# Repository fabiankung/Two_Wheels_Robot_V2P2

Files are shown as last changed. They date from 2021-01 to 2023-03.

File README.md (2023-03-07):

# Two-Wheels_Robot_V2P2 
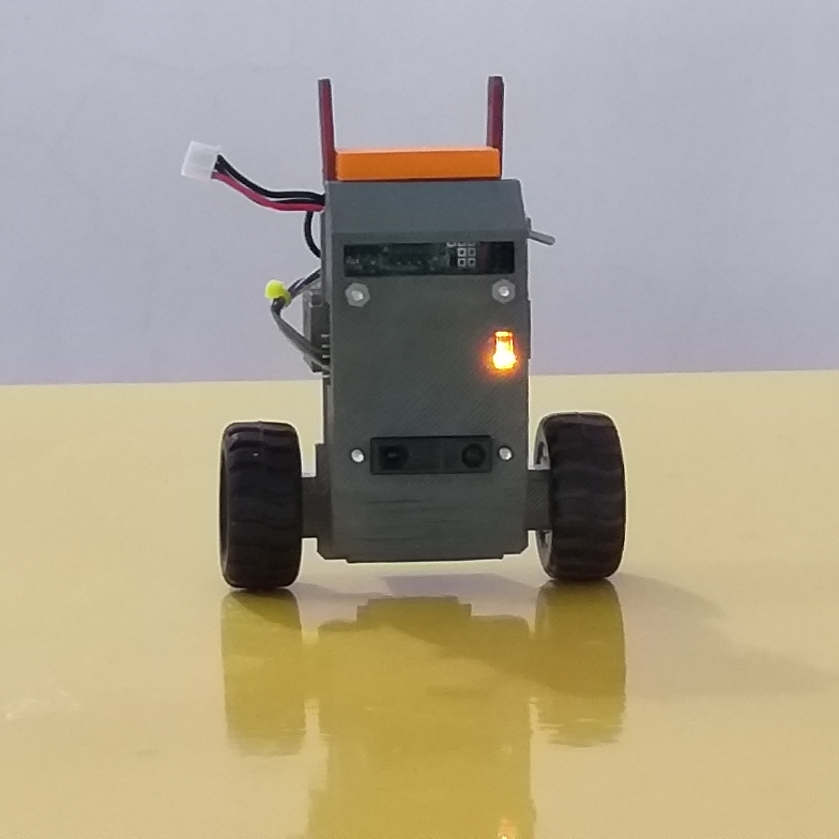
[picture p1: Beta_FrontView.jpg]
Robot Beta Version

V2P2 is a small two-wheels self-balancing mobile robot platform. It contains a single-core on-board computer as the robot controller. The robot controller handles low-level process such as sampling and processing of sensors output, implementing discrete state feedback control to balance the robot body upright and perform secondary tasks such as moving forward, turning etc. User can communicate with the robot controller through a UART port, at 3.3V CMOS logic, baud rate at 57600 bps. A simple two-way protocols allow the user controller to send instructions to the robot controller to perform simple tasks, for instance asking the robot to move at constant linear speed, turn, drive RC servo motors (the system can support up to 4 RC servos), beep a sound and many more. Thus using this robot platform, in combination with an external controller of the user, an intelligent robot system can be constructed. The external controller can be any micro-controller board capable of working with 5V supply and consuming not more than 100 mA current. Examples are Arduino Nano, Micro, Mini-Pro and Arduino Pro-micro.

In this repository, the following files are provided:
1. Getting started guide.
2. Serial communication protocol between the Robot Controller and User Controller.
3. Using Arduino Nano or Micro as the user controller, examples to communicate with the Robot Controller.
4. Andriod APK file for apps to control the V2P2 robot platform directly via Bluetooth.
5. 3D STL files of the mechanical design.
6. The schematic and PCB layout of the main circuit board. The PCB is a 4-layers board.
7. The firmware for the micro-controller.

More details will be provided in future [To do: wiring diagram].
For more robot videos please see: https://www.youtube.com/@fkungms/videos

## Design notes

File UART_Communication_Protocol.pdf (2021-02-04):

Version: 0.991
Last Update: 4 Feb 2021

/// Baud Rate: 57600 (default) or 115200.
/// Data packet: 8-bits, 1 stop bit and no parity bit.
/// --- Command packet from External Controller (EC) ---
/// [Command] + [Argument1] + [Argument2] + [Argument3] + [Argument4] + [Newline Character] /// The Newline character corresponds to 0x0A.
///
/// --- Reply to EC ---
/// If [Command] is G:
/// [Descripon] + [Hundredth] + [Tenth] + [Digit] + [Newline Character]
/// Where [Descripon] indicates the type of parameters being reported back. ///
/// Else:
/// "OK" or "NO", each string ends with [Newline Character]

Notes:
[ ] – Denotes a byte (8-bits unsigned).
[‘a’] – Denotes sending one byte, with the ASCII value of character a.
[3] + [5] – Denotes sending two bytes, first byte has a value of 3, and second byte a value of 5.
[*] – Don’t care, the value in this byte is not used, can just set it to 0.
Master | Slave | Remarks
[‘S’]+[t1]+[t2]+[t3]+[Vol]+[‘\ n’] Example: Beep tones 1, followed by 6, and 2, at volume seng 5. "S1625" | OK NO | Beep a series of 3 tones. t1, t2, t3 = ‘1’ to ‘9’, ‘1’ corresponds to lowest pitch, and ‘9’ to the highest pitch. Vol = Volume, ‘0’ to ‘5’, ‘0’ turns off the buzzer, ‘5’ is the highest volume.
[‘X’]+[*]+[*]+[*]+[*]+[‘\n’] Example: "X0000" | OK NO | Cancel all movments, stop the robot if it is moving or turning.
[‘F’]+[D]+[S0]+[*]+[*]+[‘\n’] Example: Move forward at slow speed. "F+100" | OK NO | Move at fix velocity. D = Direcon, ‘-’ for backward, any other value for forward. S0 = Speed seng, from ‘1’ (slow) to ‘4’ (very fast).
[‘M’]+[ID]+[D]+[A1]+[A0]+[‘\ n’] Example: Turn motor 0 sha to +10 degrees. "M0+10" | OK NO | Set servo motor to a specific absolute angle given by A1, A0. ID = Motor ID, currently support 0 to 2 (3 motors) D = Direcon, ‘-’ or any other values for ‘+’, with respect to center posion of motor sha. A1 = turn degree, tenth, ‘0’ to ‘9’. A0 = turn degree, unit, ‘0’ to ‘9’.
[‘D’]+[ID]+[D]+[A0]+[*]+[‘\n’] Example: Turn motor 0 sha | OK NO | Set servo motor to A1 degree relave to current sha posion. ID = Motor ID, current support 0 to 2.

1

to +8 degrees from current posion. "D0+80" | | D = Direcon, ‘-’ or any other values for ‘+’, with respect to current posion of motor sha. A0 = relave turn degree, unit, ‘0’ to ‘9’.
[‘T’]+[D]+[A2]+[A1]+[A0]+[‘\ n’] Example: Turn le 5 degrees. "T+005" | OK NO | Turn by a fix degree. D = Turn direcon, ‘-’ right, any other value le. A2 = turn degree, hundreth, ‘0’ to ‘9’. A1 = turn degree, tenth, ‘0’ to ‘9’. A0 = turn degree, unit, ‘0’ to ‘9’.

[‘G’]+[P]+[*]+[*]+[*]+[‘\n’]

Example: Request robot
plaorm to send back binary packet containing robot vital parameters.
"Gb000"

For P = ‘D’, ‘B’, ‘F’,
‘V’, ‘A’:
[P]+[V2]+[V1]+[V0]+
[‘\n’]

Where
V2 = Hundredth, ‘0’
to ‘9’.
V1 = Tenth, ‘0’ to ‘9’.
V0 = Unit, ‘0’ to ‘9’.

For P = ‘R’:
“OK” or “NO”

For P = ‘b’:
‘b’ (byte0) +
[Robot_Mode*]
(byte1) +
[Tit angle -127 to +
127] (byte2) +
[Heading upper 8
bits](byte3) +
[Heading lower 8
bits](byte4) +
[Front distance
sensor output, 0-
255mm](byte5) +
[Distance move
upper 8 bits](byte6)
+
[Distance move
lower 8 bits](byte7)

Get robot plaorm parameters. The values return depends on the nature of hardware on the robot.
P = Type of parameter:
‘D’ – Front distance sensor output, 0 to 255. ‘B’ – Baery level, 0 to 255.
‘F’ – Firmware version. Three characters.
‘R’ – Robot plaorm status, “OK” or “NO”. ‘A’ – Tilt angle, “-99” to “+99” in degree.
‘V’ – Wheels average velocity, “-99” to “+99”. 20 units = 1.0 revoluon per second.
‘b’ – Send robot plaorm parameters in binary packet instead of ASCII characters.

*bit3-0 represents the Robot Mode. Bit4 indicates whether Robot Controller is in manual (0) or auto mode (1). Bit 5 indicates whether the Robot plaorm collides
with object or not (based on stability indices signature).
Bit 6 indicates whether the Robot plaorm move or not, either voluntarily or involuntarily.

2

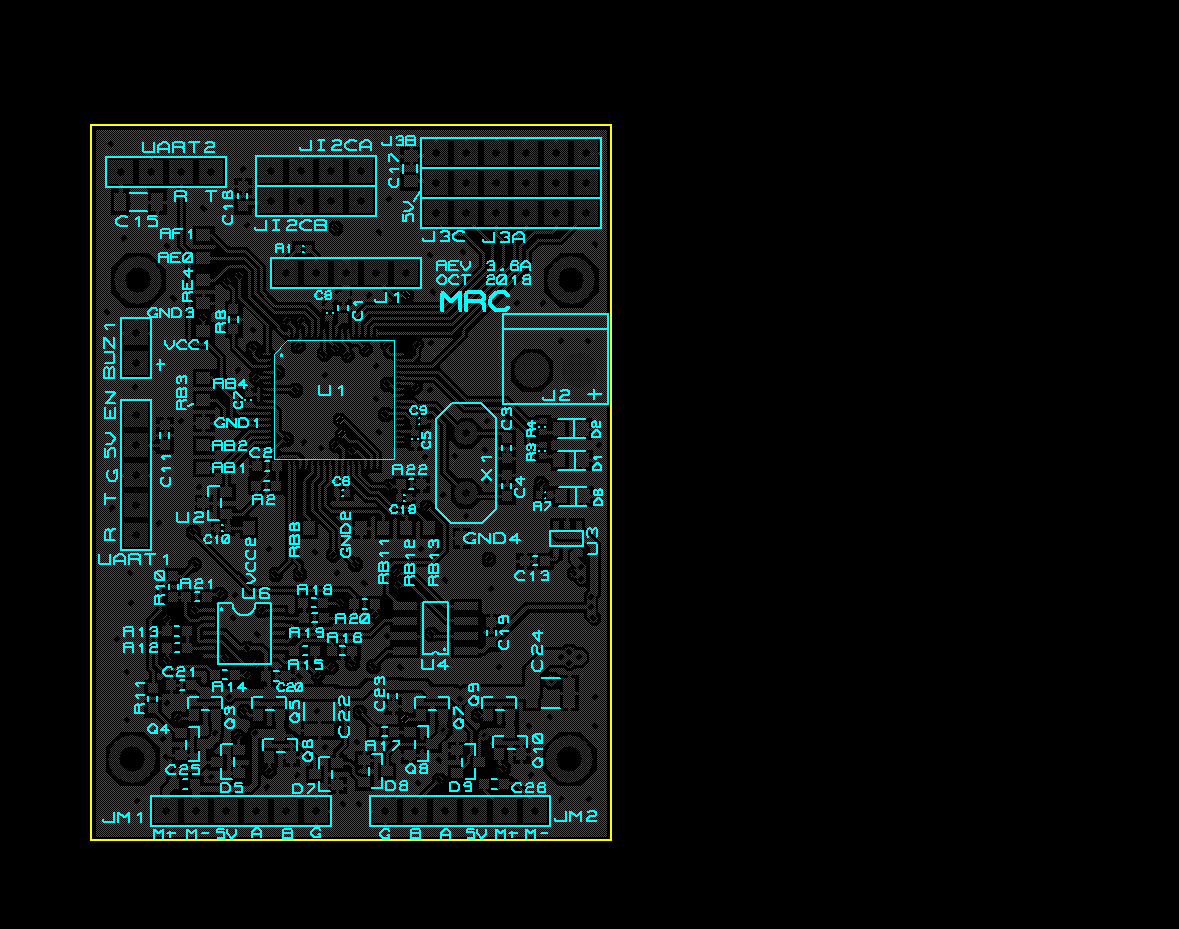
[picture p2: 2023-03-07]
Schematic_PCB/PCB_Top.bmp

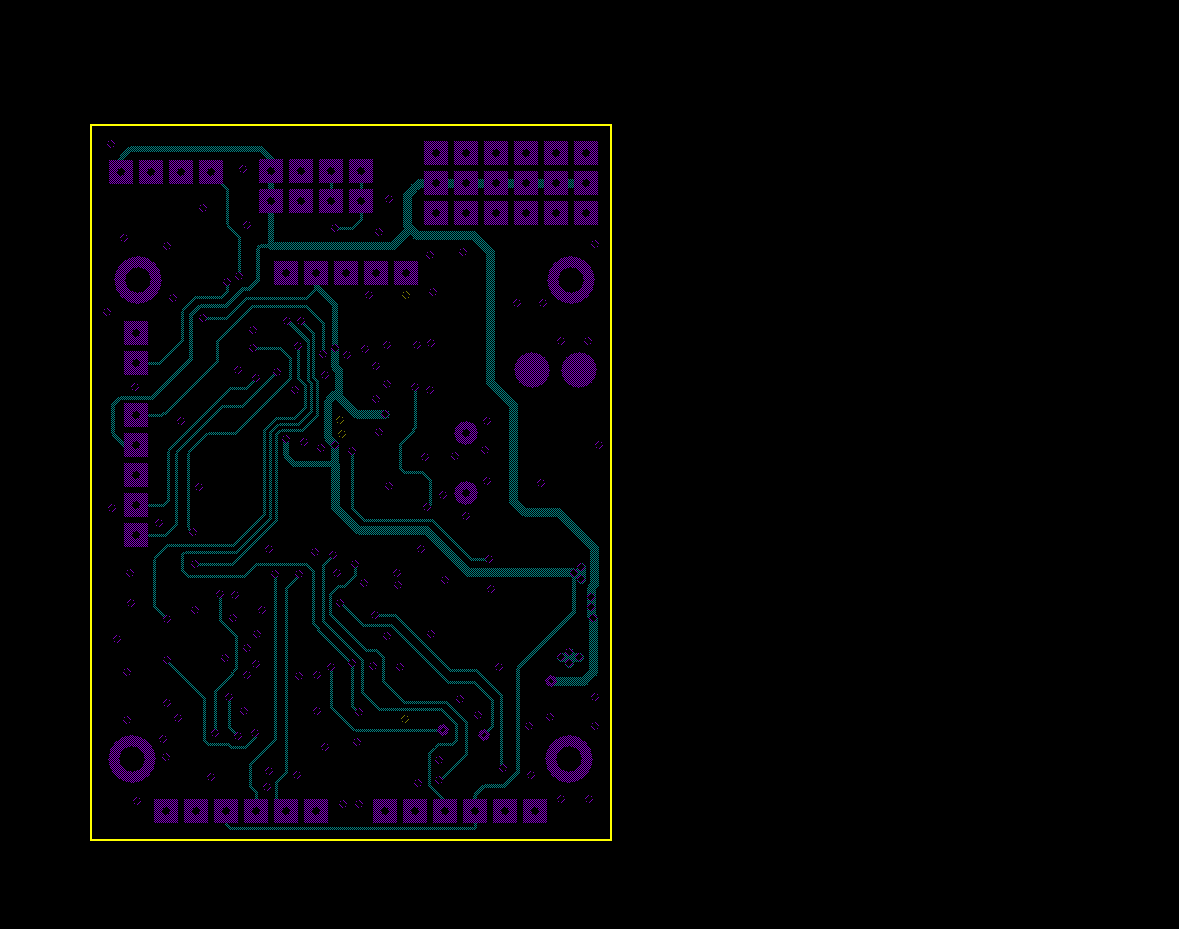
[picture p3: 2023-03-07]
Schematic_PCB/PCB_Inner2.bmp

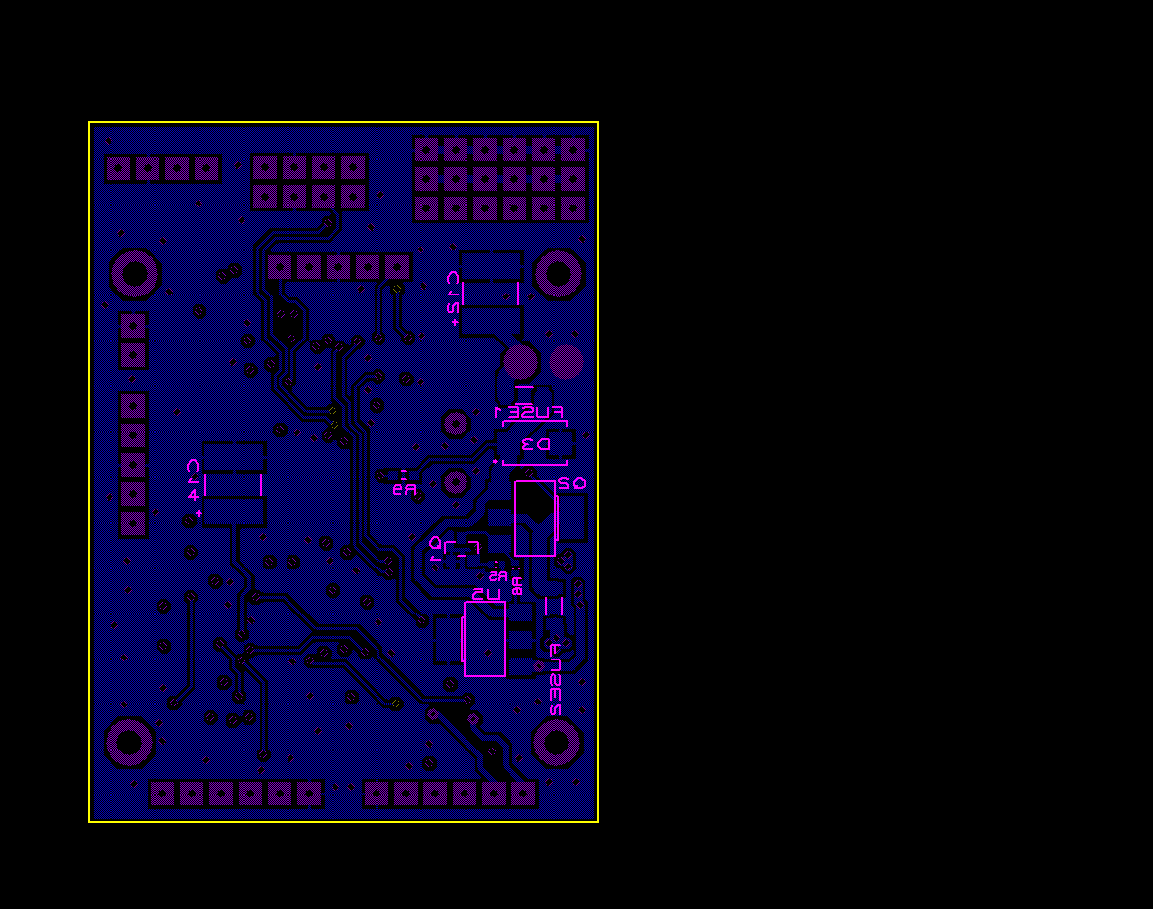
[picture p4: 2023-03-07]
Schematic_PCB/PCB_Bottom.bmp

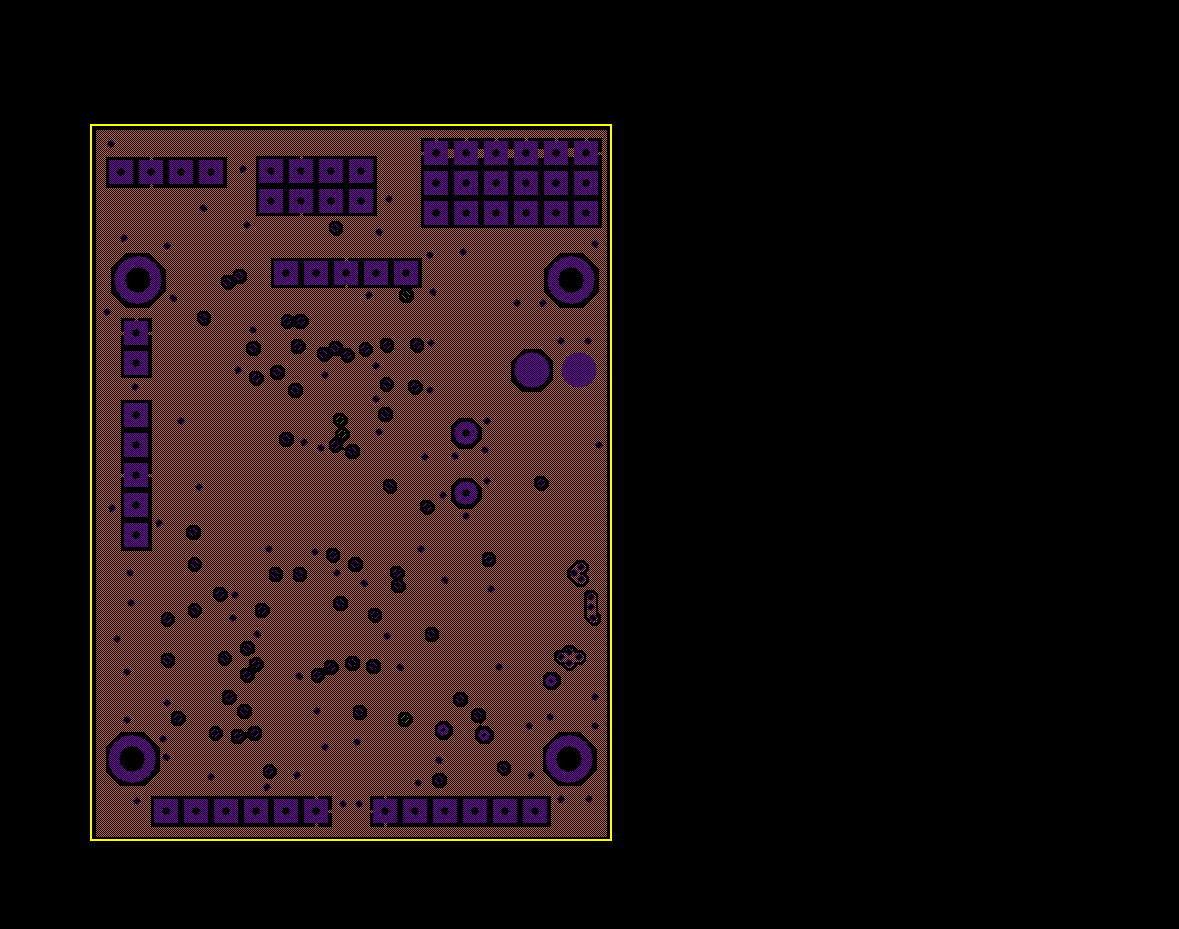
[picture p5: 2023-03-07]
Schematic_PCB/PCB_Inner1.bmp

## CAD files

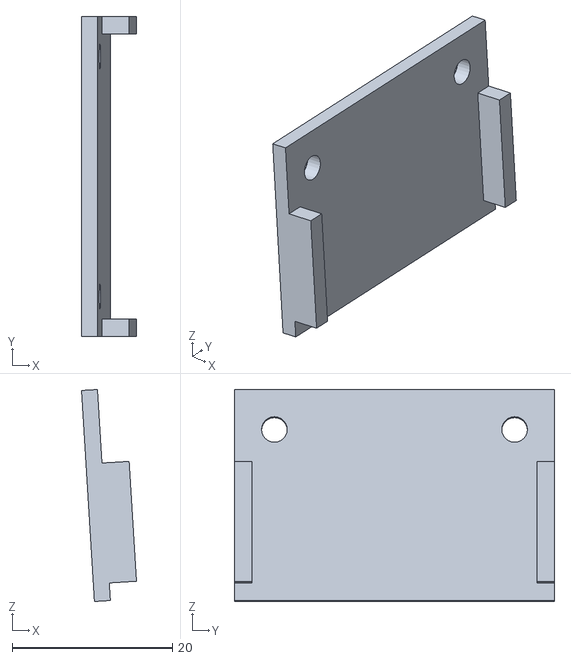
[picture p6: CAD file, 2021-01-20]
3D_Printer_Designs/Main_Body_RevB1_Top.stl
6.87 x 40.0 x 26.5

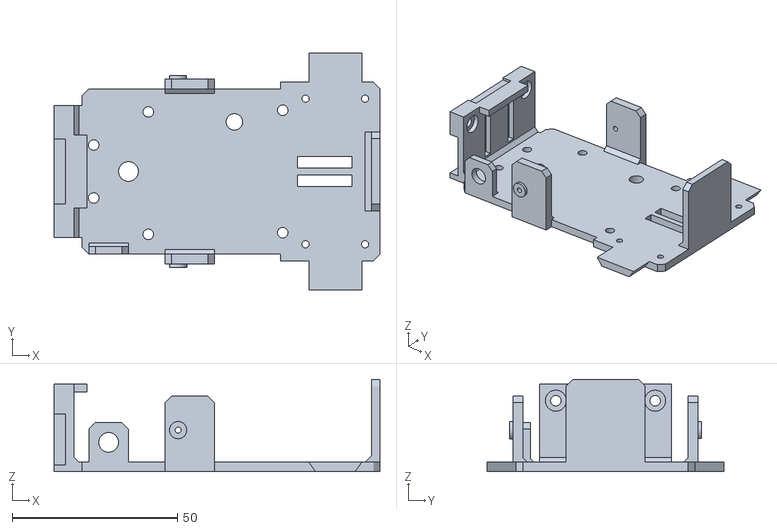
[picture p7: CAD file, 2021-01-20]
3D_Printer_Designs/Main_Body_RevB1.stl
98.5 x 71.6 x 27.8

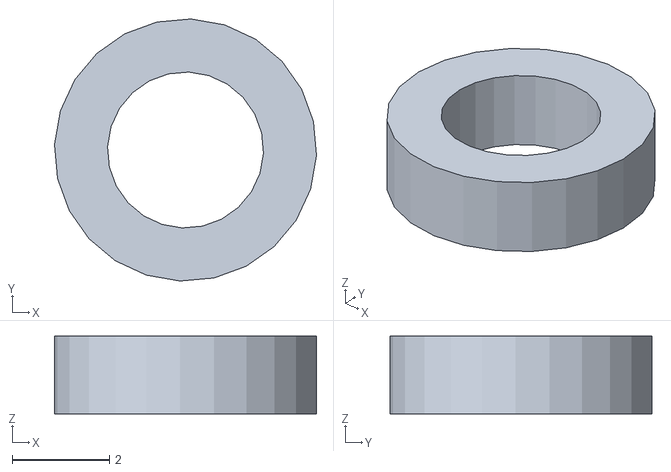
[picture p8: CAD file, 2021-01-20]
3D_Printer_Designs/Spacer_Short.stl
5.40 x 5.40 x 1.60

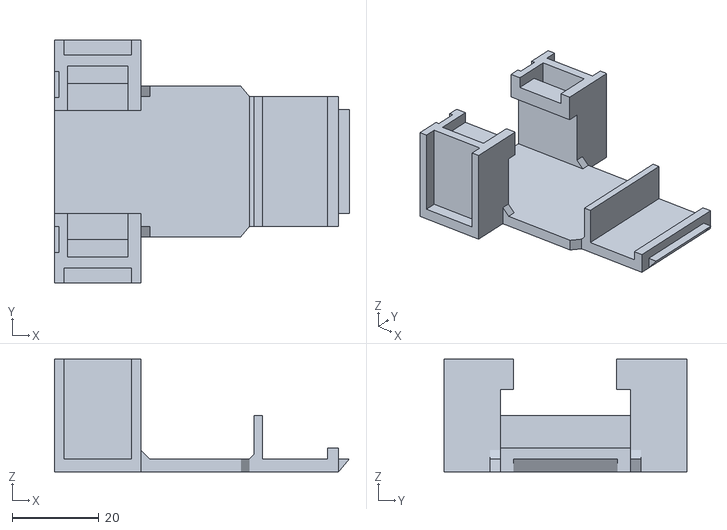
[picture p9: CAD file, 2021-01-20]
3D_Printer_Designs/BatteryHolder_RevB1.stl
68.1 x 56.0 x 26.0

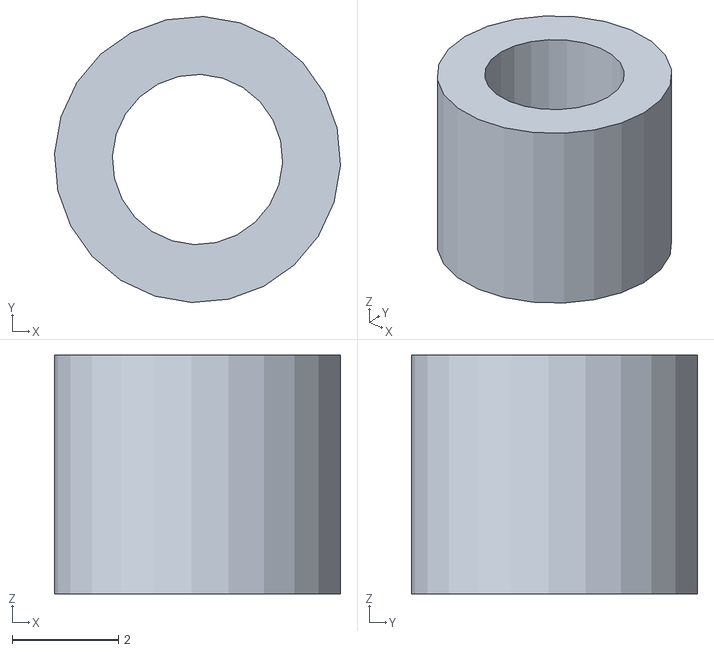
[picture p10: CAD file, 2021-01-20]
3D_Printer_Designs/Spacer_Medium.stl
5.40 x 5.40 x 4.50

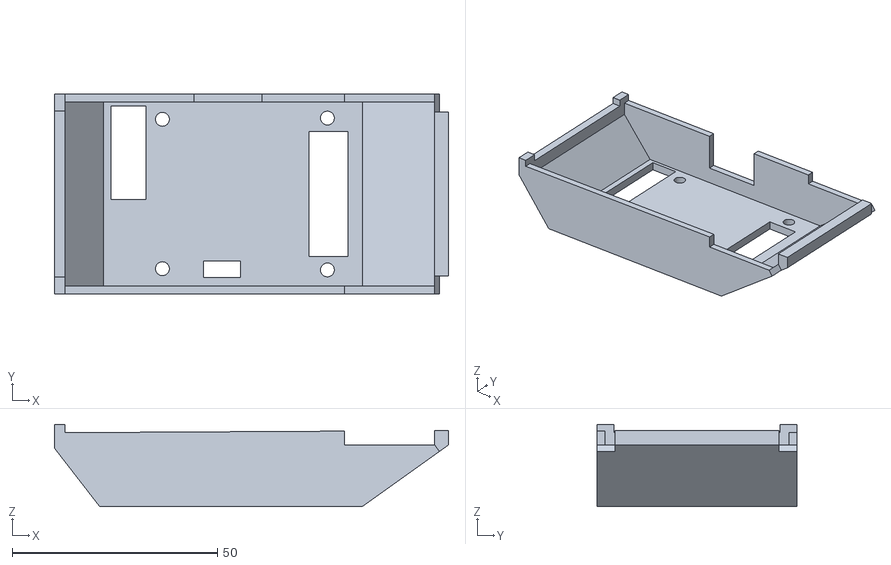
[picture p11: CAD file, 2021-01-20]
3D_Printer_Designs/Front_Cover_RevB1.stl
96.0 x 48.8 x 20.0

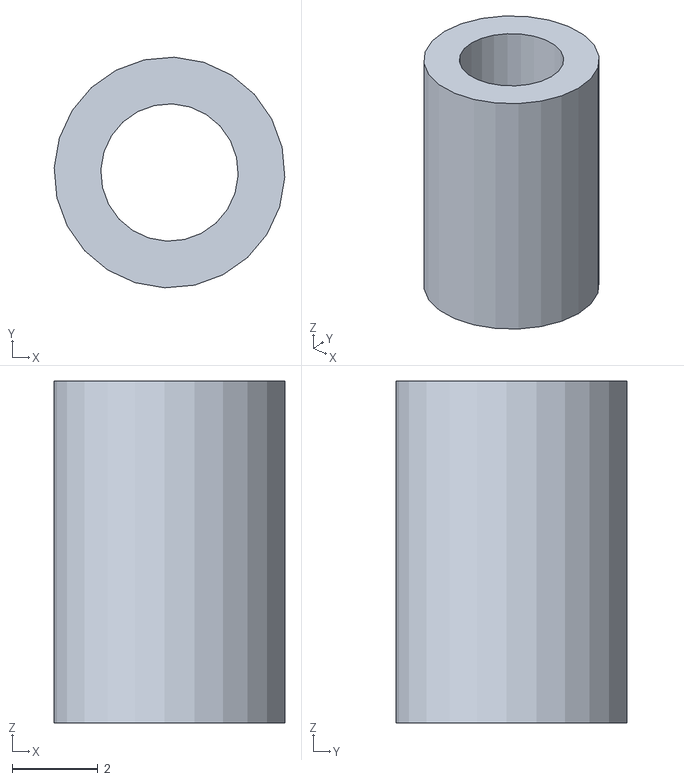
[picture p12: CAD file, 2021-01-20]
3D_Printer_Designs/Spacer_Long.stl
5.40 x 5.40 x 8.00

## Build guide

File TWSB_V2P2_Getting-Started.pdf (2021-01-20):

# TWO-WHEELS SELF-BALANCING ROBOT V2P2 AND ROBOT CONTROLLER V3.6

### Getting Started

Two-Wheel Robot V2P2 (Dec
2020)

1

# The Robot Controller (V3.6)

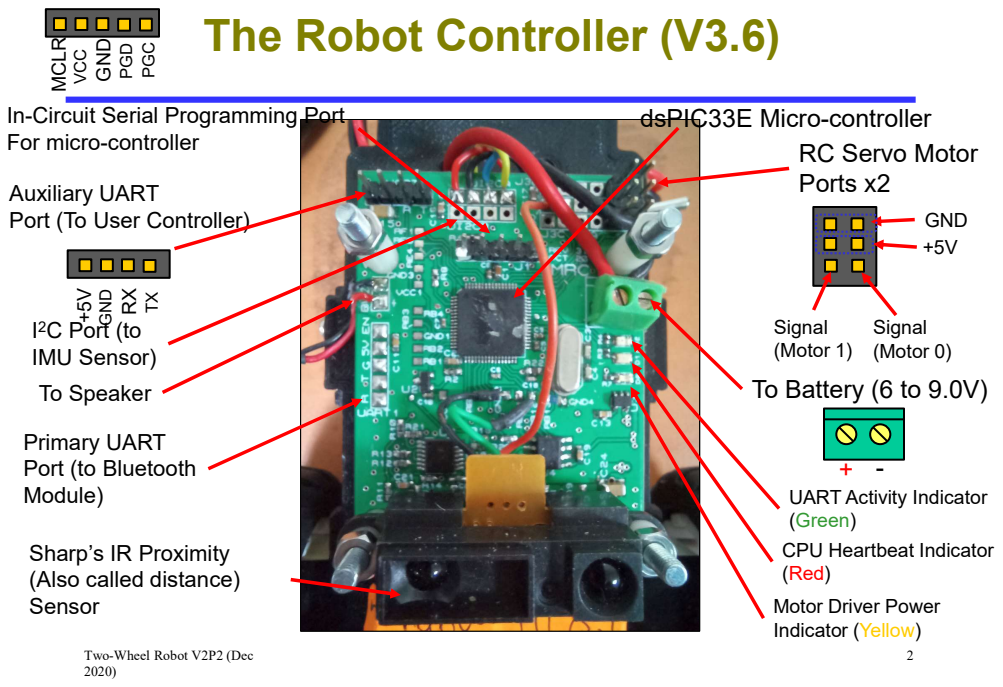
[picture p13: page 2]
GND +5V; Signal (Motor 0); In-Circuit Serial Programming Port; dsPIC33E Micro-controller

For micro-controller +5V GNDRXTX MCLR VCC GND PGD PGC

RC Servo Motor
Ports x2

Auxiliary UART
Port (To User Controller)

I²C Port (to
IMU Sensor)
To Speaker

Signal
(Motor 1)
To Battery (6 to 9.0V)

Primary UART
Port (to Bluetooth
Module)

+ - UART Activity Indicator

(Green)
CPU Heartbeat Indicator
(Red)
Motor Driver Power
Indicator (Yellow)

Sharp’s IR Proximity
(Also called distance)
Sensor

Two-Wheel Robot V2P2 (Dec

# The Inertial Measurement Unit (IMU)

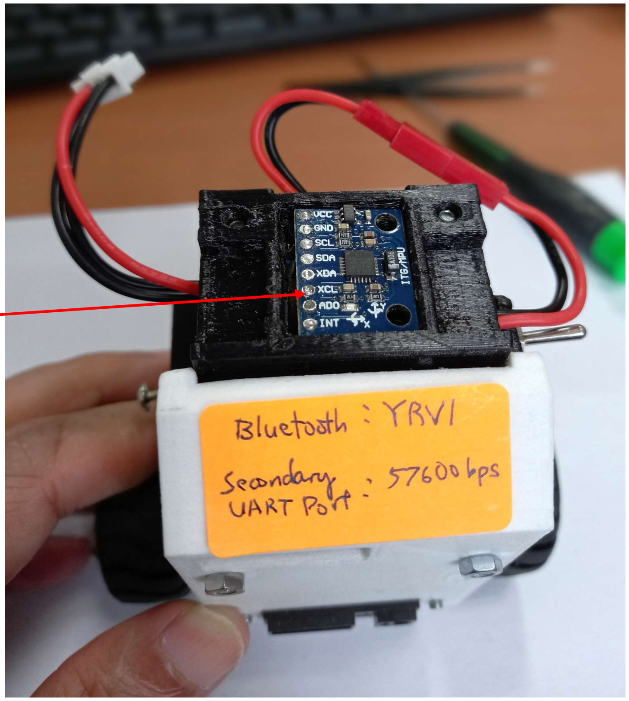
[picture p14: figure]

Two-Wheel Robot V2P2 (Dec
2020)

3

MPU6050

# PCB Top and Bottom View

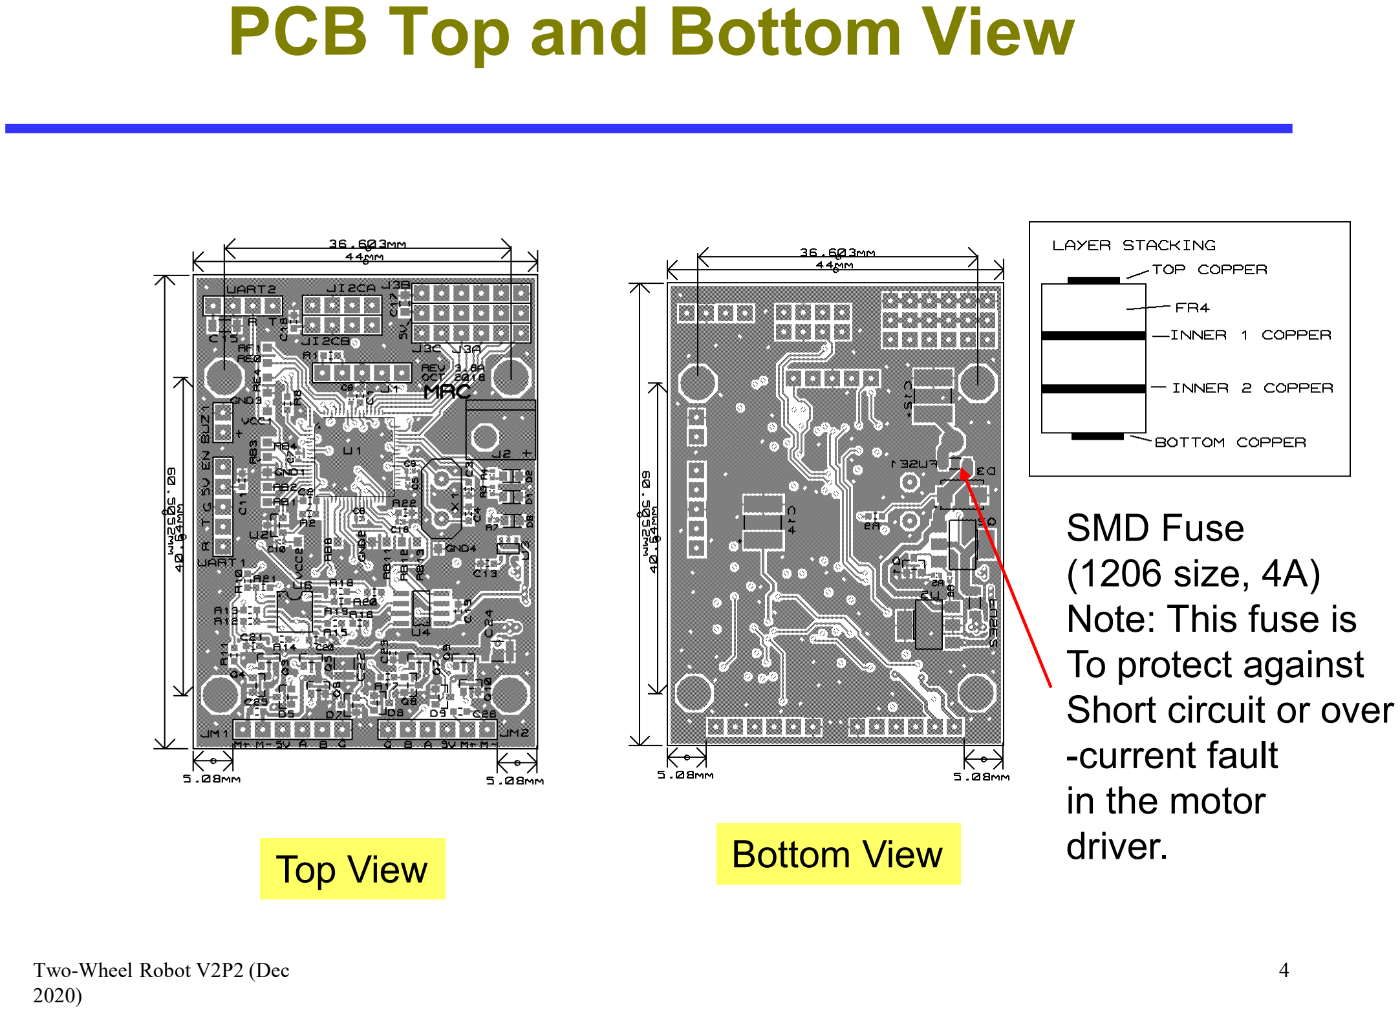
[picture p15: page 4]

Two-Wheel Robot V2P2 (Dec
2020)

4

SMD Fuse
(1206 size, 4A)
Note: This fuse is
To protect against
Short circuit or over
-current fault
in the motor
driver. Top View | Bottom View

# Example – Connecting Arduino Micro and RC Servo Motor to the Robot Controller

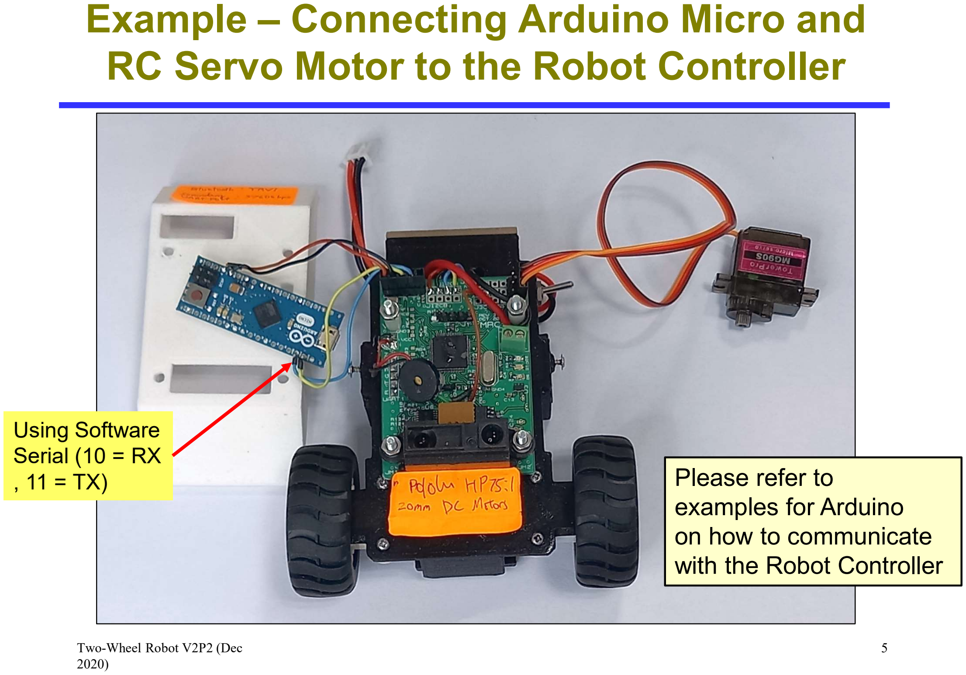
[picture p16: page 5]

Two-Wheel Robot V2P2 (Dec
2020)

5

Using Software
Serial (10 = RX
, 11 = TX) | Please refer to
| examples for Arduino
| on how to communicate
| with the Robot Controller

# Maintenance – Removing the LiPo Battery Pack

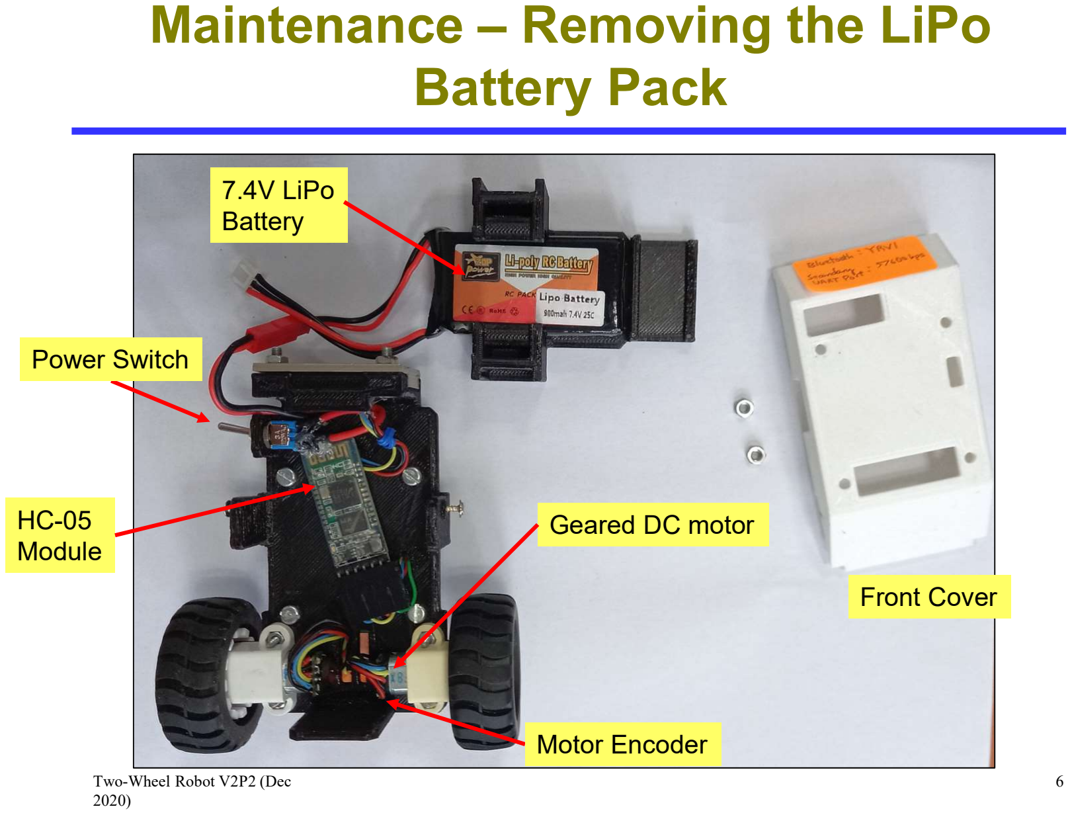
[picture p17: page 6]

Two-Wheel Robot V2P2 (Dec
2020)

6

HC-05
Module

Power Switch

Geared DC motor

Motor Encoder

7.4V LiPo
Battery

Front Cover

# Maintenance – Lubricating the Motor Gearbox

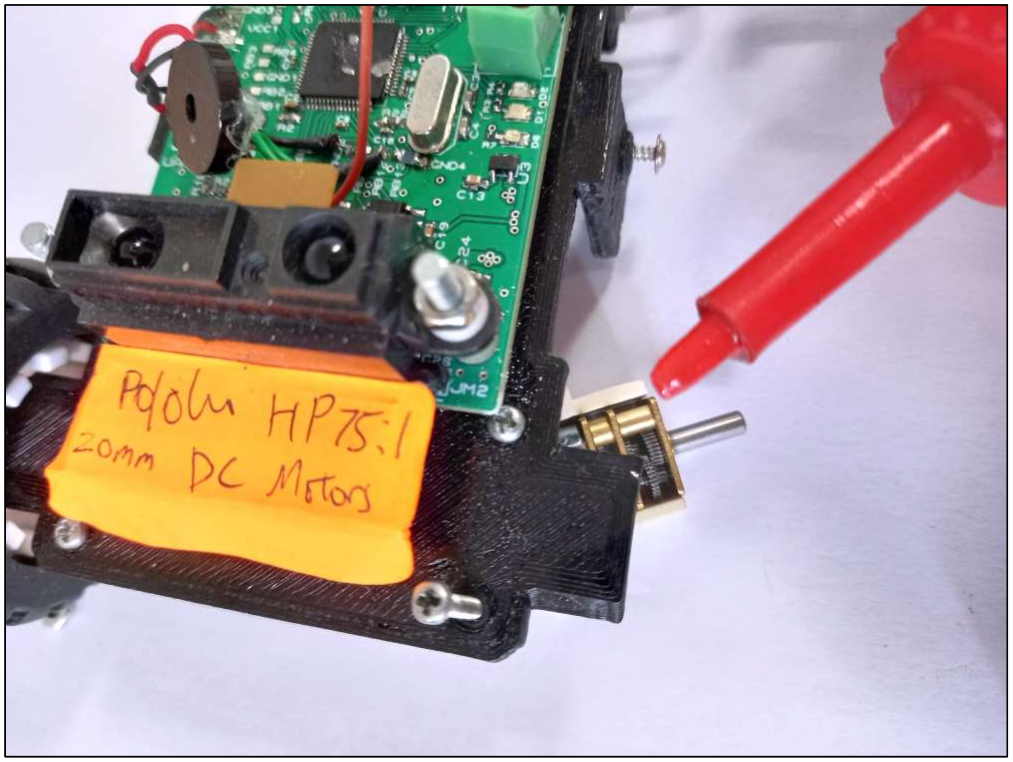
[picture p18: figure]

Two-Wheel Robot V2P2 (Dec
2020)

7

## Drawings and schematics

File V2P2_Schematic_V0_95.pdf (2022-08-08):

## Indicator 1

C11

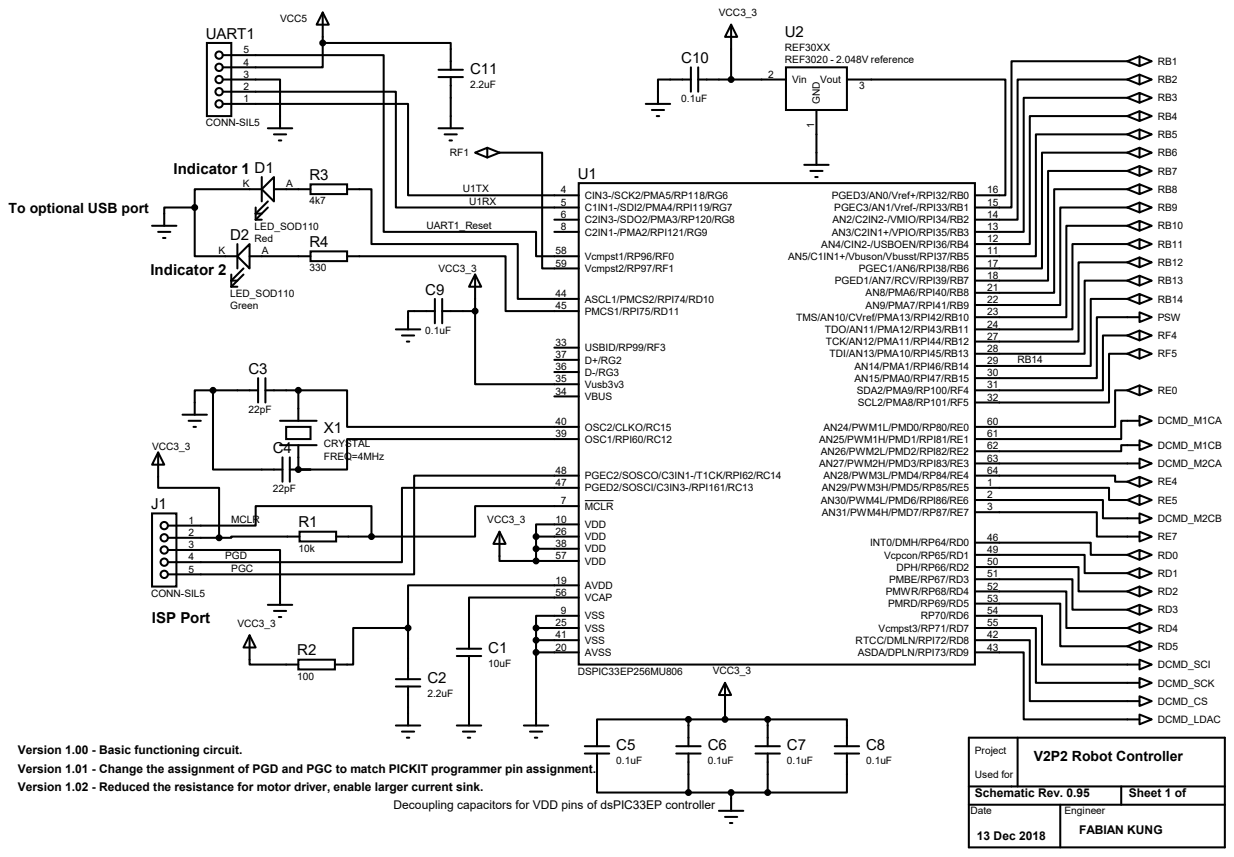
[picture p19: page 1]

To optional USB port

Version 1.00 - Basic functioning circuit.
Version 1.01 - Change the assignment of PGD and PGC to match PICKIT programmer pin assignment.
Version 1.02 - Reduced the resistance for motor driver, enable larger current sink.

Project Used for | V2P2 Robot Controller

Schematic Rev. 0.95 | Sheet 1 of
Date | Engineer FABIAN KUNG 13 Dec 2018

Decoupling capacitors for VDD pins of dsPIC33EP controller

R21

R12

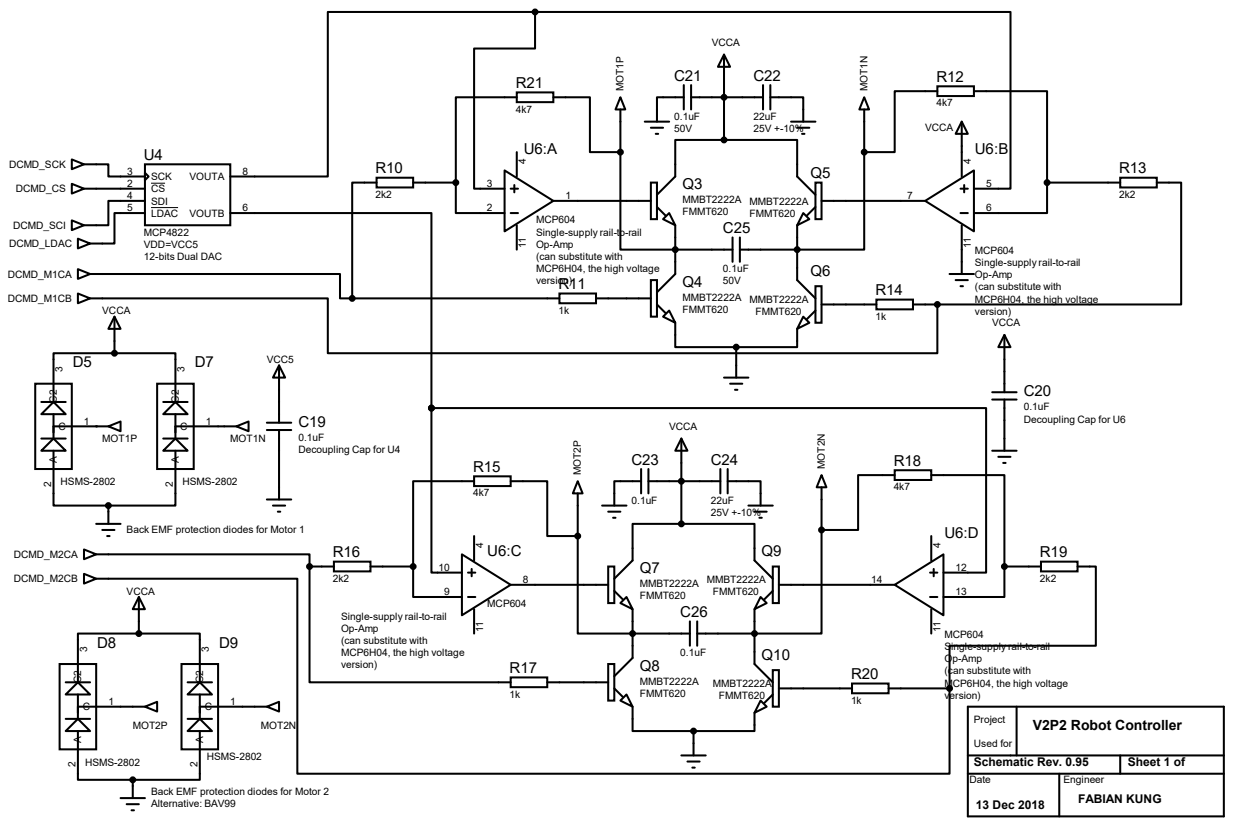
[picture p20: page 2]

MCP604
Single-supply rail-to-rail
Op-Amp
(can substitute with
MCP6H04, the high voltage
version)

VCCA

Back EMF protection diodes for Motor 1 C²

Project Used for | V2P2 Robot Controller

Schematic Rev. 0.95 | Sheet 1 of
Date | Engineer FABIAN KUNG 13 Dec 2018

U3

J3A

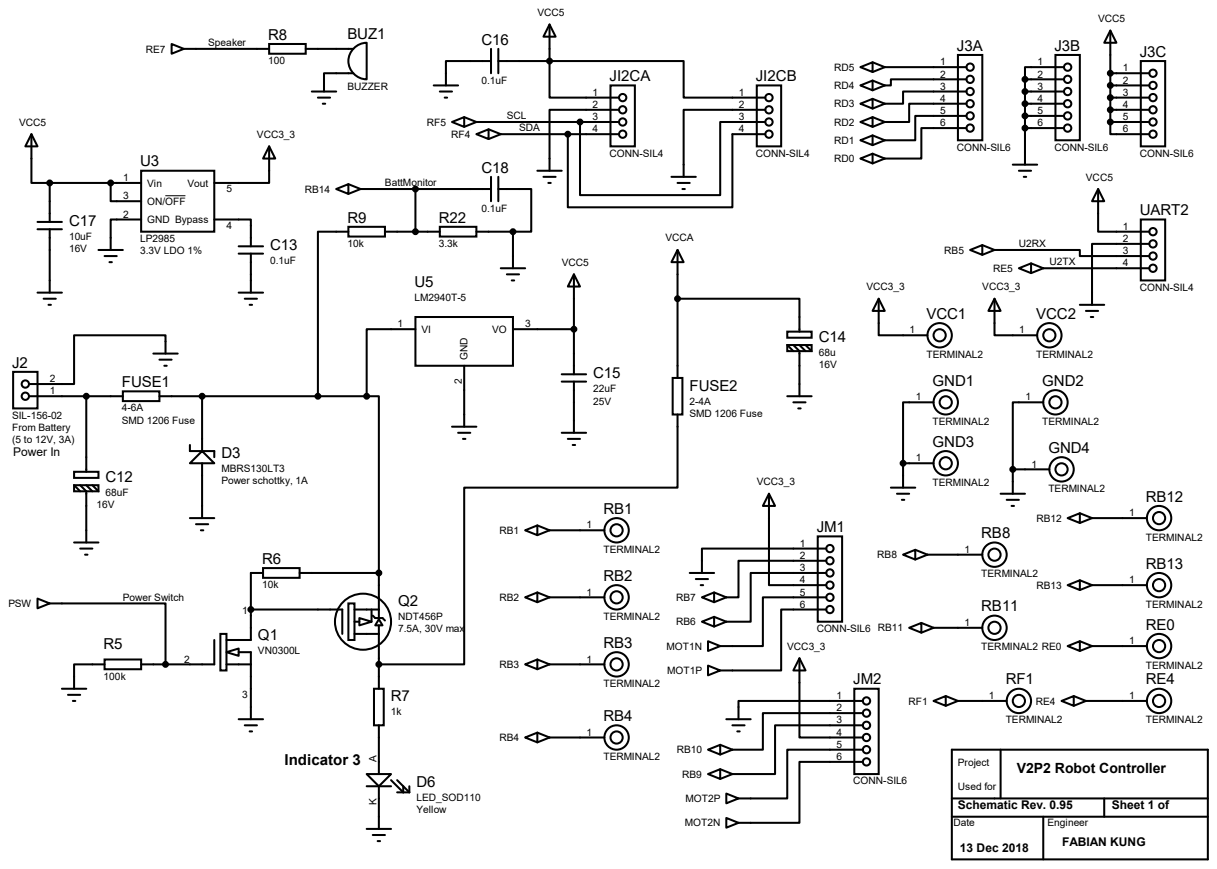
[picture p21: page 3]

Project Used for | V2P2 Robot Controller

Schematic Rev. 0.95 | Sheet 1 of
Date | Engineer FABIAN KUNG 13 Dec 2018

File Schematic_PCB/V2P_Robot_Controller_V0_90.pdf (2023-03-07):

## Indicator 1

C11

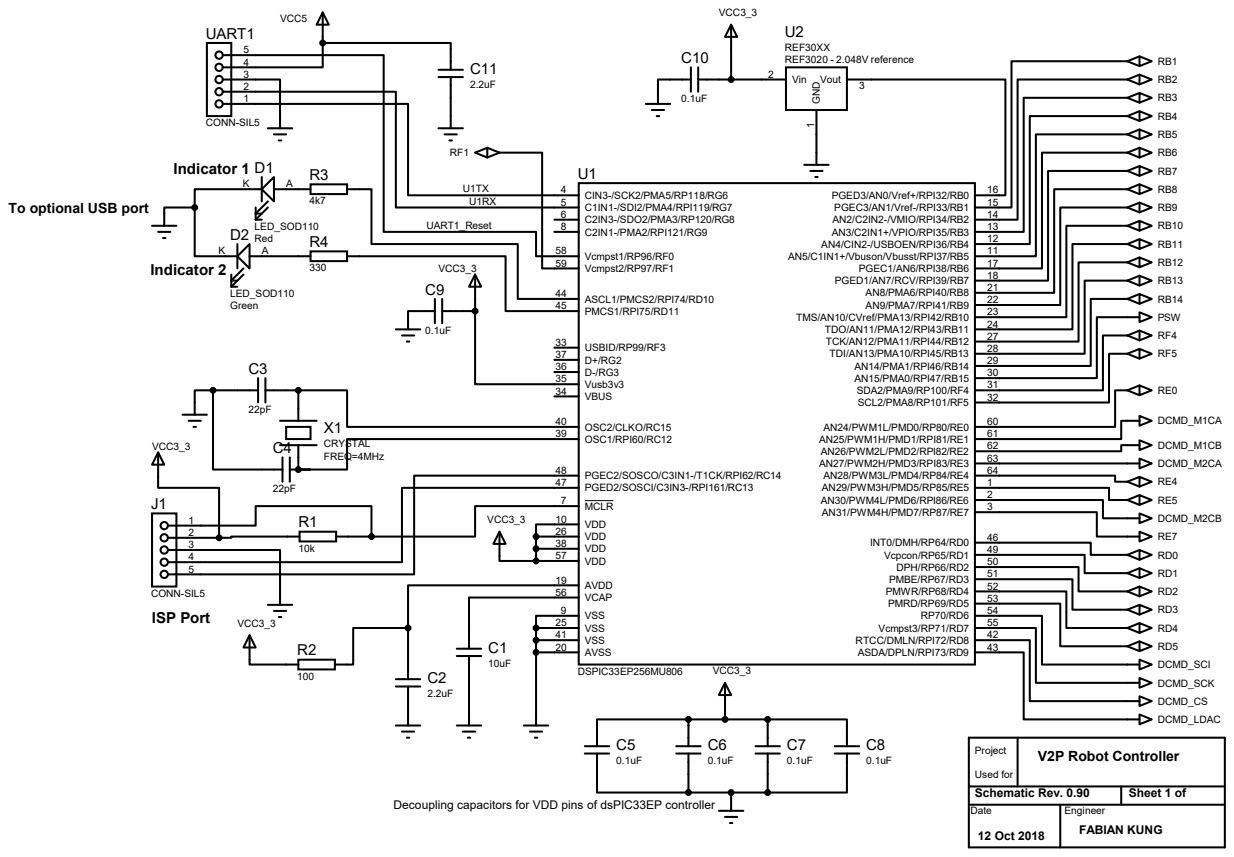
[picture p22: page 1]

To optional USB port

Project Used for | V2P Robot Controller

Schematic Rev. 0.90 | Sheet 1 of
Date | Engineer FABIAN KUNG 12 Oct 2018

Decoupling capacitors for VDD pins of dsPIC33EP controller

R21

R12

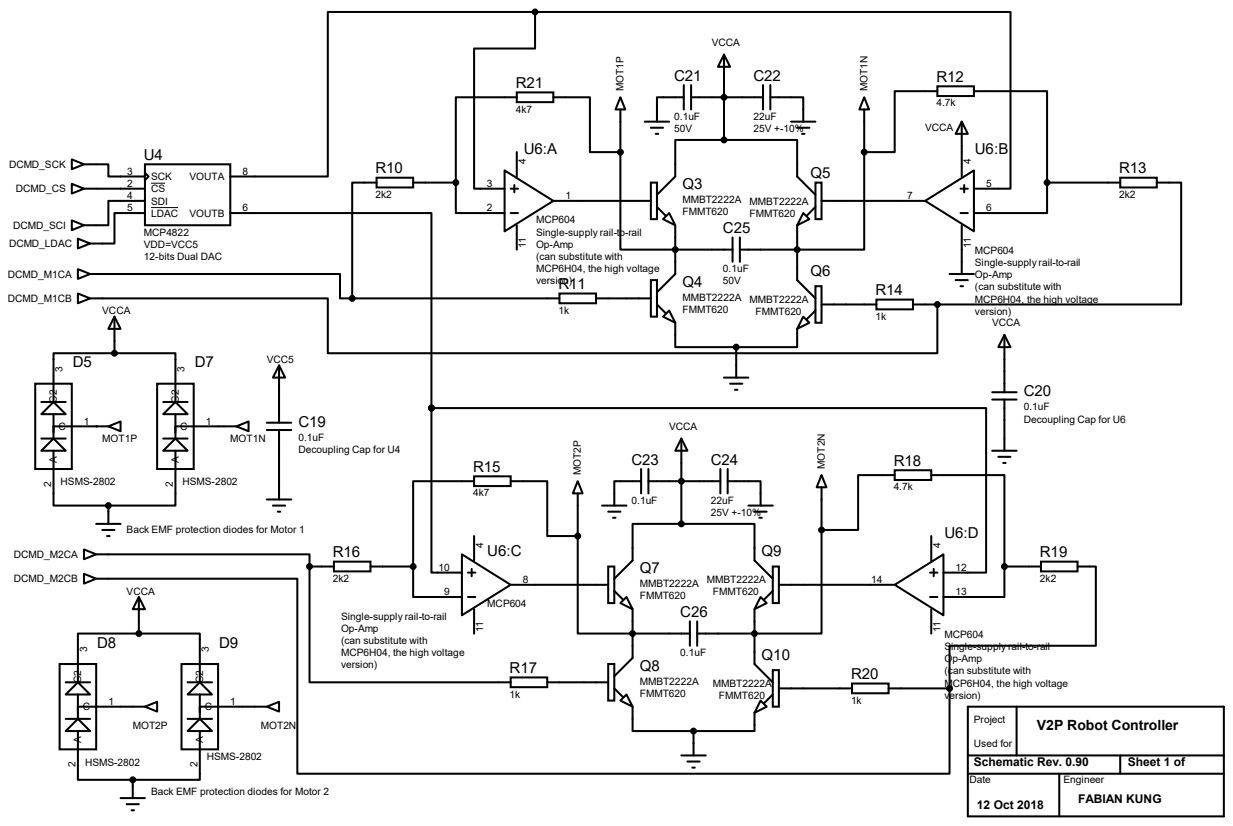
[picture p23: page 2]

MCP604
Single-supply rail-to-rail
Op-Amp
(can substitute with
MCP6H04, the high voltage
version)

VCCA

Back EMF protection diodes for Motor 1 C²

Project Used for | V2P Robot Controller

Schematic Rev. 0.90 | Sheet 1 of
Date | Engineer FABIAN KUNG 12 Oct 2018

U3

J3A

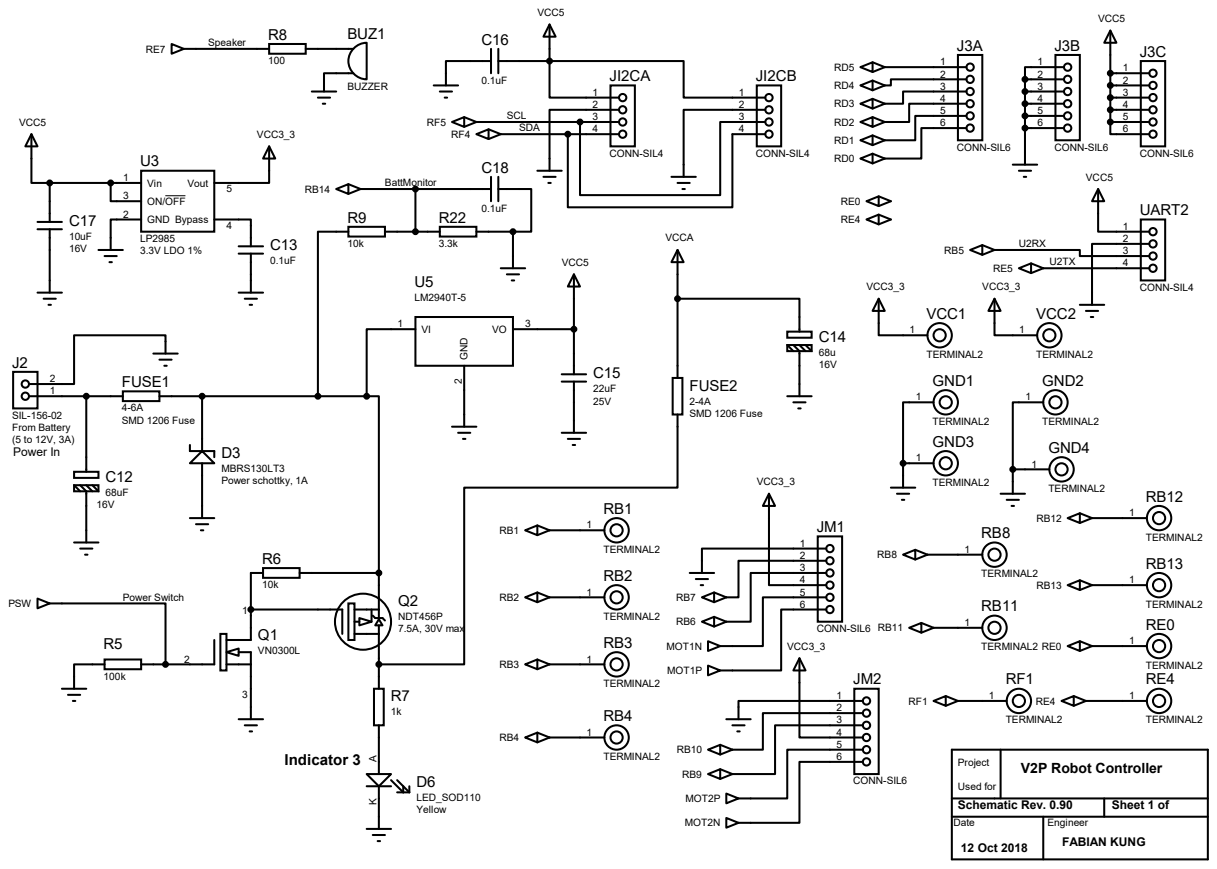
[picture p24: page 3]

Project Used for | V2P Robot Controller

Schematic Rev. 0.90 | Sheet 1 of
Date | Engineer FABIAN KUNG 12 Oct 2018

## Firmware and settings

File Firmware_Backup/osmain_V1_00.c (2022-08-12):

///////////////////////////////////////////////////////////////////////////////////////////////////
//
//	BASIC REAL-TIME OPERATING SYSTEM (RTOS) FOR 8/16-BITS MICROCONTROLLER
//
//
//  (c) Copyright 2013-2019, Fabian Kung Wai Lee, Selangor, MALAYSIA
//  All Rights Reserved  
//   
///////////////////////////////////////////////////////////////////////////////////////////////////
//
// Filename         : osmain_V1_00.c
// Author(s)		: Fabian Kung
// Last modified	: 13 March 2019
// Release Version	: 1.06 (This refers to OS version or release)
// Description		: Main C file for the RTOS.
//                    Uses round-robin scheduling algorithm to schedule tasks.
// Toolsuites		: Microchip MPLAB X IDE v5.10 or above
//                	  MPLAB XC16 C-Compiler v1.33 or above
//                    Microchip Pickit3 or ICD3
// Microcontroller	: dsPIC33EP256MU806 16-bits, 64 pins, 28kbyte RAM, 256kbyte Flash ROM, 70 MIPS.
// Oscillator/Clock	: 4 MHz crystal (XT mode) with Phase-Locked Loop multiplier to 140 MHz (70 MIPS)
//					  
// Main Features:
// 1) Up to 70 MIPS.
// 2) Multi-tasking with Round-robin equal priority scheduler.
// 3) Hardware watchdog timer.
// 4) Systick timer.
// 5) Ability to assign a timer for all processes, resolution of 1 Systick.
// 6) 3x Wired serial communication (UART) interface stacks.
// 7) 1x I2C serial communication interface stack.
// 8) Wireless RF communication stack using IEEE 802.15.4 or Bluetooth.
// 9) Include a new Resource Usage Summary table, giving an overview of controller and external circuits
//    resources usage, pin usage etc.
// 10) Better task error tracking.  This version includes two error tracking features, in which
//     the processor will hang whenever one of the following errors is encountered:
//     a) When OSSetTaskContext() is not called before the task pass control back to the 
//     Scheduler.
//     b) In the case of task using state-machine architecture, the default state is called.
//     This indicates a wrong state is assigned in the codes, hence the state-machine look-up
//     mechanism cannot find a correct state, and assign the current execution to the default
//     state.
//
// Minimum Directory and file structures:
// C library routines for various drivers/peripherals:
// 1. <path for library>\C_Library\dsPIC33E\
// Files needed: "osmain.h", "os_API.c" and "os_dsPIC33E_API.c"
// 2. <Project folder>\os "osmain.c" codes and user files.
//

///////////////////////////////////////////////////////////////////////////////
// --- INCLUDE ALL DRIVER AND USER HEADER FILES --- ///////////////////////////
///////////////////////////////////////////////////////////////////////////////

// Include common header to all drivers and sources.  Here absolute path is used for library source.
// To edit if one change folder.

// Main header file.  All source codes should include this.
#include "C:\Users\User\Google Drive\Projects\Embedded_Systems\C_Library\dsPIC33E\osmain.h"
// Header file for each driver used.

#include "C:\Users\User\Google Drive\Projects\Embedded_Systems\C_Library\dsPIC33E\Driver_ADC_DAC_V100.h"
#include "C:\Users\User\Google Drive\Projects\Embedded_Systems\C_Library\dsPIC33E\Driver_Audio_V101.h"
#include "C:\Users\User\Google Drive\Projects\Embedded_Systems\C_Library\dsPIC33E\Driver_UART1_V100.h"
#include "C:\Users\User\Google Drive\Projects\Embedded_Systems\C_Library\dsPIC33E\Driver_PWMServo_V101.h"
#include "C:\Users\User\Google Drive\Projects\Embedded_Systems\C_Library\dsPIC33E\Driver_I2C_V100.h"
#include "C:\Users\User\Google Drive\Projects\Embedded_Systems\C_Library\dsPIC33E\Bluetooth_HC_05\Driver_HC_05_V100.h"
#include "C:\Users\User\Google Drive\Projects\Embedded_Systems\C_Library\dsPIC33E\Driver_UART2_V100.h"
#include "C:\Users\User\Google Drive\Projects\Embedded_Systems\C_Library\dsPIC33E\Driver_QuadEncoder_V100.h"
// Header file user routines.
#include ".\Robot_Tasks_dsPIC33E.h"
///////////////////////////////////////////////////////////////////////////////

// --- MAIN LOOP ---

INT16 main(void)
{
	INT16 ni = 0;

	OSEnterCritical();			// Disable and store all processor's interrupt setting.
	OSEnterCritical();			// Do this twice to prevent interrupt happen midway, and the 
                                // processor interrupt is re-enabled upon return from the 
                                // interrupt service routine.
	dsPIC33E_PORInit(140);		// Power-on Reset initialization for the controller, set processor
                                // clock speed to 140 MHz.
	OSInit();                   // Initialize the RTOS.
	gnTaskCount = 0; 			// Initialize task counter.
//
//								// Initialize core OS processes.
	OSCreateTask(&gstrcTaskContext[gnTaskCount], OSProce1);  // Start blinking LED.
								// User and other non-core OS tasks are initialized 
								// here.
//	OSExitCritical();			// Enable all processor interrupts (optional, some processor 
								// interrupts are turned on within PIC24H_PORInit or dsPIC33_PORInit
								// routines, thus it is not necessary for now).

///////////////////////////////////////////////////////////////////////////////
// --- CREATE AN INSTANCE OF DRIVER AND USER TASKS HERE --- ///////////////////
///////////////////////////////////////////////////////////////////////////////

        //OSCreateTask(&gstrcTaskContext[gnTaskCount], Robot_Claw_Driver);            // 15, for use with V2T2.  If V2T1 this should be disabled.
        
        // NOTE: DO NOT EXCEEED THE MAXIMUM LIMIT SET BY  __MAXTASK in file "osmain.h".
	// Kernel Driver tasks:
        OSCreateTask(&gstrcTaskContext[gnTaskCount], Proce_UART1_Driver);           // 1
        OSCreateTask(&gstrcTaskContext[gnTaskCount], Proce_UART2_Driver);           // 2    
        OSCreateTask(&gstrcTaskContext[gnTaskCount], Proce_ADC_Driver);             // 3
        OSCreateTask(&gstrcTaskContext[gnTaskCount], Proce_12DAC_MCP4822_Driver);   // 4
        OSCreateTask(&gstrcTaskContext[gnTaskCount], Proce_Audio_Driver);           // 5
        OSCreateTask(&gstrcTaskContext[gnTaskCount], Proce_BT_HC_05_CommStack);     // 6 , HC-05 Bluetooth module driver/communication stack.
        OSCreateTask(&gstrcTaskContext[gnTaskCount], Proce_PWMServo_Driver);        // 7
        OSCreateTask(&gstrcTaskContext[gnTaskCount], Proce_I2C_Driver);             // 8
        OSCreateTask(&gstrcTaskContext[gnTaskCount], Proce_QuadEncoder_Driver);     // 9
        OSCreateTask(&gstrcTaskContext[gnTaskCount], Robot_ExControllerMessageLoop);     // 10
	// Robot/User tasks:
        OSCreateTask(&gstrcTaskContext[gnTaskCount], User_ProceTest2);               // 11, Experimental, to deactivate when not used.
        OSCreateTask(&gstrcTaskContext[gnTaskCount], User_Proce1);                  // 12
        OSCreateTask(&gstrcTaskContext[gnTaskCount], Robot_Sensor_MPU6050_CF);      // 13
        //OSCreateTask(&gstrcTaskContext[gnTaskCount], Robot_Sensor_MPU6050_KF);      // 13
        OSCreateTask(&gstrcTaskContext[gnTaskCount], Robot_Balance);                // 14
        OSCreateTask(&gstrcTaskContext[gnTaskCount], Robot_MoveTurn);               // 15
        OSCreateTask(&gstrcTaskContext[gnTaskCount], Robot_MoveLinear);             // 16
        OSCreateTask(&gstrcTaskContext[gnTaskCount], Robot_Proce1);                 // 17
///////////////////////////////////////////////////////////////////////////////

    while (1)				// Infinite loop.
    {
        ClearWatchDog();		// Clear the Watch Dog Timer.
        if (gnRunTask > 0) 		// Only execute tasks/processes when gnRunTask is not 0.
        {                   
            //_RB1 = 1;                               // Trigger debug flag.
            for (ni = 0; ni < gnTaskCount; ni++)    // Inspect the task attribute of each process.
            {
                if (gstrcTaskContext[ni].nTimer > 0) // Only decrement timer if it is greater than zero.
                {
                    --(gstrcTaskContext[ni].nTimer); // Decrement timer for each process.
                }
                // Only execute a process/task if it's timer = 0.
                if (gstrcTaskContext[ni].nTimer == 0)
                {	
                    gunTaskExecutedCount++;
                    // Execute user task by dereferencing the function pointer.
                    (*((TASK_POINTER) gfptrTask[ni]))(&gstrcTaskContext[ni]);
                }
            }
            gnRunTask = 0; 		// Reset gnRunTask.        
            //_RB1 = 0;                               //
        }
    }
    return 0;
}

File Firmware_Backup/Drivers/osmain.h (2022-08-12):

// Author			: Fabian Kung
// Date				: 24 Aug 2020
// Filename			: osmain.h

///////////////////////////////////////////////////////////////////////////////////////////////////
//  BEGINNING OF CODES SPECIFIC TO dsPIC33E MICROCONTROLLER        ////////////////////////////////
///////////////////////////////////////////////////////////////////////////////////////////////////

#ifndef __OSMAIN_H
#define __OSMAIN_H

// --- Microcontroller specific header file (provided by compiler manufacturer) ---

#include <xc.h>     // This header file will allow access to all include files.
                    // Recommended by Microchip, and also to conform to the practice
                    // of code portability, via the concept of Common C Interface (CCI).
                    // The header file for the microcontroller will be automatically
                    // included with this header file.

#define DSPIC33E_PAGELENGTH 1024    // Page length for dsPIC33E family,
                                    // 1024 24-bits instruction words in one page.
#define DSPIC33E_ROWLENGTH 128      // Row length for dsPIC33E family,
                                    // 128 24-bits instruction words in one row.

// --- Mapping of variable datatype to match the controller's architecture ---
#define	INT16 	int                 // 16-bits signed integer.
#define INT32   long                // 32-bits signed integer.
#define	UINT16	unsigned int		// 16-bits unsigned integer.
#define UINT32  unsigned long		// 32-bits unsigned integer.
#define	BYTE	unsigned char		// 8-bits unsigned integer.

// --- Microcontroller I/O Pin definitions ---
#define	PIN_OSPROCE1            _RD10 		// Indicator LED1 driver pin.
#define	PIN_ILED2               _RD11 		// Indicator LED2 driver pin.
#define PIN_PSW                 _RB15       // Analog power supply switch control.

// --- Processor Clock and Kernel Cycle in microseconds ---
// Note: Uncomment the required value for _TIMER1COUNT, and update the corresponding definition
// for the constant _SYSTEMTICK_US, in microseconds.

/*
// - For 120 MHz oscillator - 
#define	__FOSC_MHz              120             // Oscillator clock frequency in MHz.
#define __FCYC_MHz              __FOSC_MHz*0.5  // Processor frequency = 60 MHz.
#define	__TCLK_US               0.01667         // Processor clock = fosc/2 = fcyc for dsPIC33E.
                                                // Tclk = 1/60000000 = 1.667E-08.
                                                // Tcyc = (_TIMER1COUNT*(Tclk))= 166.67 usec
*/

/*
// - For 124 MHz oscillator -
#define	__FOSC_MHz              124             // Oscillator clock frequency in MHz.
#define __FCYC_MHz              __FOSC_MHz*0.5  // Processor frequency = 62 MHz.
#define	__TCLK_US               0.016129        // Processor clock = fosc/2 = fcyc for dsPIC33E.
                                                // Tclk = 1/62000000 = 1.61290-08.
                                                // Tcyc = (_TIMER1COUNT*(Tclk))= 166.67 usec
*/

/*
// - For 128 MHz oscillator -
#define	__FOSC_MHz              128             // Oscillator clock frequency in MHz.
#define __FCYC_MHz              __FOSC_MHz/2    // Processor frequency = 64 MHz.
#define	__TCLK_US               0.015625        // Processor clock = fosc/2 = fcyc for dsPIC33E.
                                                // Tclk = 1/64000000 = 1.5625-08.
                                                // Tcyc = (_TIMER1COUNT*(Tclk))= 166.67 usec
*/

// - For 132 MHz oscillator -
//#define	__FOSC_MHz              132             // Oscillator clock frequency in MHz.
//#define __FCYC_MHz              __FOSC_MHz/2    // Processor frequency = 66 MHz.
//#define	__TCLK_US               0.015152        // Processor clock = fosc/2 = fcyc for dsPIC33E.
                                                // Tclk = 1/66000000 = 1.5152-08.
                                                // Tcyc = (_TIMER1COUNT*(Tclk))= 166.67 usec

// - For 136 MHz oscillator -
//#define	__FOSC_MHz              136             // Oscillator clock frequency in MHz.
//#define __FCYC_MHz              __FOSC_MHz/2    // Processor frequency = 68 MHz.
//#define	__TCLK_US               0.014706        // Processor clock = fosc/2 = fcyc for dsPIC33E.
                                                // Tclk = 1/68000000 = 1.4706-08.
                                                // Tcyc = (_TIMER1COUNT*(Tclk))= 166.67 usec
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

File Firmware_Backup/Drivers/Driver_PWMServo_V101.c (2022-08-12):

//////////////////////////////////////////////////////////////////////////////////////////////
//
//	USER DRIVER ROUTINES DECLARATION (PROCESSOR DEPENDENT)
//
//  (c) Copyright 2013-2019, Fabian Kung Wai Lee, Selangor, MALAYSIA
//  All Rights Reserved  
//   
//////////////////////////////////////////////////////////////////////////////////////////////
//
// File             : Driver_PWMServo_V101.c
// Author(s)		: Fabian Kung
// Last modified	: 9 March 2019
// Tool suites		: Microchip MPLAB X IDE v4.05 or above
//                	  MPLAB XC16 C-Compiler v1.33 or above


// Include common header to all drivers and sources.  Here absolute path is used.
// To edit if one change folder
#include "osmain.h"

// NOTE: Public function prototypes are declared in the corresponding *.h file.


//
// --- PUBLIC VARIABLES ---
//
typedef struct StructProcePWMDriver
{
    UINT16   NumChannel;            // No. of outputs, valid values are 4, 6 and 8.  Any
                                    // other values not of these will be assume as 8 channel
                                    // of outputs.
    UINT16   unEnPWM;               // Set greater than 0 to enable the PWM module.
} DSPIC33E_PWM_DRIVER;

DSPIC33E_PWM_DRIVER    gobjDriverPWM;

// RC servo motor driver control variables
UINT16 gunRCServoPW_us[8];                  // RC servo motor pulse width in usec.
UINT16 gunPWStep_us[8];                     // RC servo motor pulse width increment/decrement
                                            // step in usec.
UINT16 gnCurrentMotorIDA = 0;               // Current ID of RC servo motor being triggered.
UINT16 gunRCServoStat[8] = {0,0,0,0,0,0,0,0}; // Status of RC servo motor.
                                            // 0 - Motor reached position, i.e. the pulse width is similar to the
                                            // required value, or the motor is not moving.
                                            // Otherwise - Motor is still moving towards target angle.
//
// --- PRIVATE FUNCTION PROTOTYPES ---
//


//
// --- PRIVATE VARIABLES ---
//


//
// --- Microcontroller Pin Usage ---
//
// RD0 = Servo motor 0                                         
// RD1 = Servo motor 1
// RD2 = Servo motor 2
// RD3 = Servo motor 3
// RD4 = Servo motor 4
// RD5 = Servo motor 5
// RF4 = Servo motor 6
// RF5 = Servo motor 7
// 

//
// --- Process Level Constants Definition --- 
//
#define         _MAX_PULSEWIDTH_US	2300                        // Max pulse width in microseconds.
#define         _MIN_PULSEWIDTH_US	620                         // Min pulse width in microseconds.

#define         _PWM_SERVO_MOT_CONST              __FCYC_MHz    // This is FOSC_MHz/2, which is 60 for 120 MHz clock

                                                                // For FCYC = 60MHz, this corresponds to 65535/60 = 1092.468
                                                                // or 1093, and so on.
#if             __FCYC_MHz == 60    
    #define         _PWM_SERVO_SINGLE_COUNTER_LIMIT     1093
#elif           __FCYC_MHz == 62
    #define         _PWM_SERVO_SINGLE_COUNTER_LIMIT     1057
#elif           __FCYC_MHz == 64
    #define         _PWM_SERVO_SINGLE_COUNTER_LIMIT     1024
#elif           __FCYC_MHz == 66
    #define         _PWM_SERVO_SINGLE_COUNTER_LIMIT     993
#elif           __FCYC_MHz == 68
    #define         _PWM_SERVO_SINGLE_COUNTER_LIMIT     964
#elif           __FCYC_MHz == 70
    #define         _PWM_SERVO_SINGLE_COUNTER_LIMIT     936
#else
    #error "Proce__PWMServo_Driver: Processor frequency not supported"
#endif


#define         _INITIAL_PW1_US         1300           // A neutral position for the motor/actuator triggered.
#define         _INITIAL_PW2_US         1300
#define         _INITIAL_PW3_US         1300
#define         _INITIAL_PW4_US         1300
#define         _INITIAL_PW5_US         1300
#define         _INITIAL_PW6_US         1300
#define         _INITIAL_PW7_US         1300
#define         _INITIAL_PW8_US         1300

#define         _DEFAULT_PW_STEP_US     3

///
/// Process name		: Proce__PWMServo_Driver
///
/// Author              : Fabian Kung
///
/// Last modified		: 9 March 2019
///
/// Code Version		: 1.02
///
/// Processor			: 
///                       dsPIC33E256MU80X family.
///                       dsPIC33E512MC80X family.
///
/// Processor/System Resources 
/// PINS                : See above.
///
/// MODULES             : 1. OC1 - output compare 1 (Internal).
///                       2. OC2 - output compare 2 (Internal).                               
///
/// RTOS                : Ver 1 or above, round-robin scheduling.
///
/// Global variables    : gunRCServoPW - User set RC servo control pulse width.
///                       nRCServoState - RC servo driver state.

#ifdef 				  __OS_VER		// Check RTOS version compatibility.
	#if 			  __OS_VER < 1
		#error "Proce__PWMServo_Driver: Incompatible OS version"
	#endif
#else
	#error "Proce__PWMServo_Driver: An RTOS is required with this function"
#endif
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

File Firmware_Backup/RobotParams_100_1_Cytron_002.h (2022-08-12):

 /* 
 * File         : RobotParams_100_1_Cytron_002.h
 * Author       : Fabian Kung
 * Date         : 15 March 2022
 * Description  : Constants for electromechanical parameters of the robot.
 *                For production V2P2 with 100:1 HP Micro-metal gear motors
 *                from Cytron Technologies and 42mm diamater rubber wheels.
 *                Serial number V2P2002
 */

#ifndef ROBOTPARAMS1_H
#define	ROBOTPARAMS1_H

#ifdef	__cplusplus
extern "C" {
#endif

    #define     _ROBOT_VERSION_V2P2     // Robot mechanical design version.    
    #define     _HEAD_SINGLE_DOE        // The number of degree of freedom in the head.
                
// ******************* TUNABLE PARAMETERS **************************************************
    
// --- Primary parameters: State-feedback coefficients and DC motors non-linear parameters ---
   
// Here fixed point format for representing real numbers, Q8.8 format is adopted
// for the coefficients.
    
    // Coefficients with emphasis on theta and d(theta)/dt, used during standing still and 
    // small angle turning.
    #define     _FP_DEFAULT_FP      0b1111100000000000 // -8.00, Q8.8 format.
    #define     _FKX_DEFAULT_FP     0b1111110100000000 // -3.00, Q8.8 format.
    #define     _FKV_DEFAULT_FP     0b1111110000000000 // -4.00, Q8.8 format.
    #define     _FCW_DEFAULT_FP     0b1111111110110010 // -0.30469, Q8.8 format.
    #define     _R_DEFAULT_FP       0b0000000000000011 // 0.01172, Q8.8 format.
    #define     _L_MOT_OFFSET_DEFAULT_FP    0b0100000000000000 // +64.00, Q8.8 format.
    #define     _R_MOT_OFFSET_DEFAULT_FP    0b0100000000000000 // +64.00, Q8.8 format.    

    /*
    #define     _FP_DEFAULT_FP      0b0000000000000000 // 0.00, Q8.8 format.
    #define     _FKX_DEFAULT_FP     0b0000000000000000 // 0.00, Q8.8 format.
    #define     _FKV_DEFAULT_FP     0b0000000000000000 // 0.00, Q8.8 format.
    #define     _FCW_DEFAULT_FP     0b0000000000000000 // 0.00, Q8.8 format.
    #define     _R_DEFAULT_FP       0b0000000000000000 // 0.00, Q8.8 format.
    #define     _MOS_DEFAULT_FP     0b0000001000000000 // +2.00, Q8.8 format.
    #define     _L_MOT_OFFSET_DEFAULT_FP    0b0010000000000000 // +32.00, Q8.8 format.
    #define     _R_MOT_OFFSET_DEFAULT_FP    0b0010000000000000 // +32.00, Q8.8 format.       
     */
// Tuning interval, represented in Q8.8 fixed point format and floating point format.    
    
    #define     _FP_INTERVAL_FP     0b0000000001000000 // +0.25, Q8.8 format.
    #define     _FP_INTERVAL        0.25               // +0.25, floating point format.
    #define     _FKX_INTERVAL_FP    0b0000000000001000 // +0.03125, Q8.8 format.
    #define     _FKX_INTERVAL       0.03125             // +0.03125, floating point format.
    #define     _FKV_INTERVAL_FP    0b0000000000001000 // +0.03125, Q8.8 format.
    #define     _FKV_INTERVAL       0.03125             // 0.03125, floating point format.
    #define     _FCW_INTERVAL_FP    0b0000000000000100 // +0.015625, Q8.8 format.
    #define     _FCW_INTERVAL       0.015625           // +0.015625, floating point format.
    #define     _R_INTERVAL_FP      0b0000000000000001 // +0.00390625, Q8.8 format.
    #define     _R_INTERVAL         0.00390625          // +0.0078125, floating point format.
    #define     _MOS_INTERVAL_FP    0b0000001000000000 // +2, Q8.8 format.
    #define     _MOS_INTERVAL       2                  // +2.00, floating point format.    
    
// ******************* CONSTANT PARAMETERS **************************************************
    
    // Coefficients with emphasis on x and v state parameters, used during linear movement
    // and large angle or continuous turning.
    //#define     _FP_STIFF         -4.50   
    #define     _FP_STIFF         -4.25 
    //#define     _FKX_STIFF        -3.75      
    #define     _FKX_STIFF        -3.50   
    #define     _FKV_STIFF        -4.50         
    //#define     _FCW_STIFF        -0.265625  
    #define     _FCW_STIFF        -0.2890625  
    
    // Coefficients with even more emphasis on theta and d(theta)/dt state parameters, used 
    // during standing still on uneven or soft surface.
    #define     _FP_SOFT         -6.75      
    #define     _FKX_SOFT        -0.875      
    #define     _FKV_SOFT        -1.40     
    #define     _FCW_SOFT        -0.46875
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

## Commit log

2022-08-08 Add files via upload
    Schematic
2022-08-12 Add files via upload
    Driver routines for dsPIC33E family of processors peripherals.
